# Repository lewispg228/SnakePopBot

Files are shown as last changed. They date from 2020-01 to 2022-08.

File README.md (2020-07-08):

OpenSnake
========================================

<p align="center">
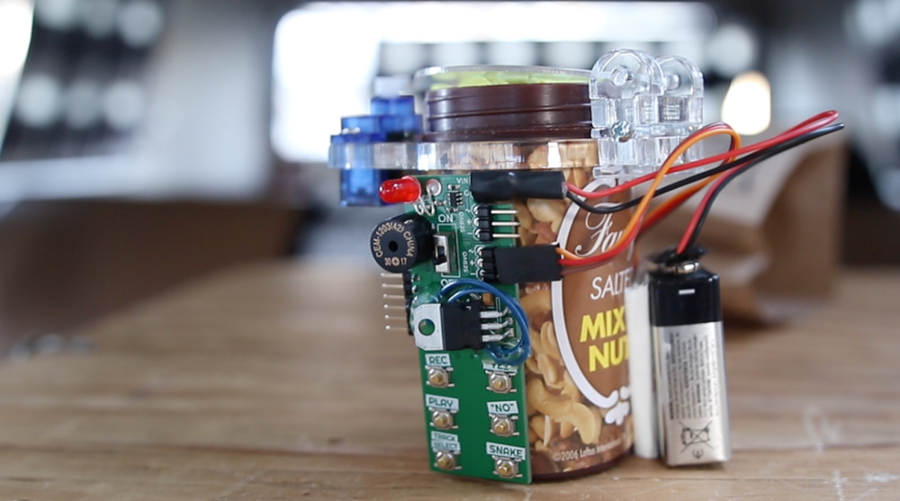
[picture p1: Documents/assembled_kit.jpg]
  
</p>

OpenSnake is the opensource firmware and design files that are used to produce the Electronic Snake In A Can Kit. It is a collaboration between Mario the Maker Magician and Jumping Snakes Engineering.

<p align="center">
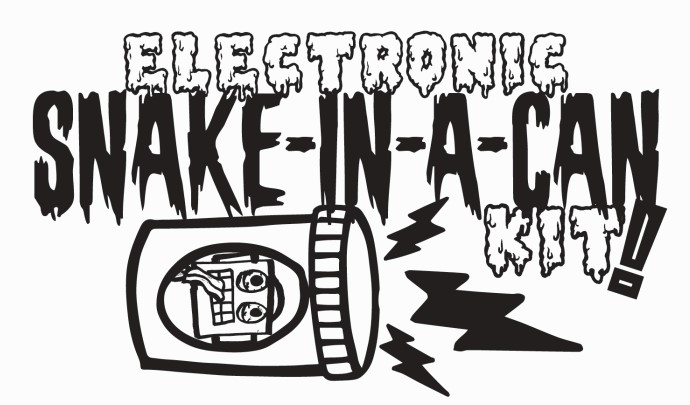
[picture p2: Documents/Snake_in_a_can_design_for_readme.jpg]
  
</p>

The classic snake-in-a-can gag meets DIY MAGIC! With this kit, you'll assemble an Electronic Snake-in-a-Can, introducing you to the world of programming, robotics, and how these tools can be used to create surprise, magic, and comedy.

* includes CONTROLLER for PLAYBACK and RECORDER of robotic magic tricks\
* RE-PROGRAMMABLE with ARDUINO
* learn about SERVOS, BUZZERS, BUTTONS, and LEDs
* pre-programmed with a magic routine written by Mario, PLUS you can make your own
* note: requires 9V battery (not included)

Buy this kit at Mario The Maker Magician's website here:

[BUY KIT HERE](https://www.mariothemagician.com/product-page/electronic-snake-in-a-can-kit)

The magic trick "skit" that is included as track one in the firmware can be watched here on Mario's Instagram post:

[INSTAGRAM VIDEO](https://www.instagram.com/tv/CCRtKZynAKZ/)

Repository Contents
-------------------

* **/Documentation** - assembly instructions, pictures, additional product information
* **/Firmware** - Arduino Code used on the snake-in-a-can controller
* **/Hardware** - Eagle design files (.brd, .sch)
* **/Hardware/Production** - Production panel files (.brd and gerbers)

License Information
-------------------

This product is _**open source**_! 

Please review the LICENSE.md file for license information. 

If you have any questions or concerns on licensing, please [file an issue on this repository](https://github.com/lewispg228/OpenSnake/issues), and we will respond asap.

Distributed as-is; no warranty is given.

- Jumping Snakes Engineering.

_<COLLABORATION CREDIT>_
  
<p align="center">
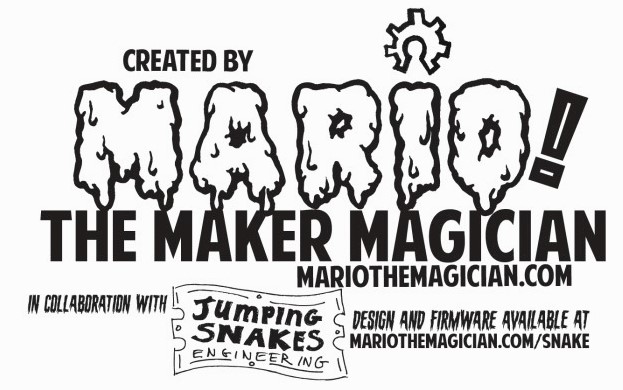
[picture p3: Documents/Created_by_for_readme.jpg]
  
</p>

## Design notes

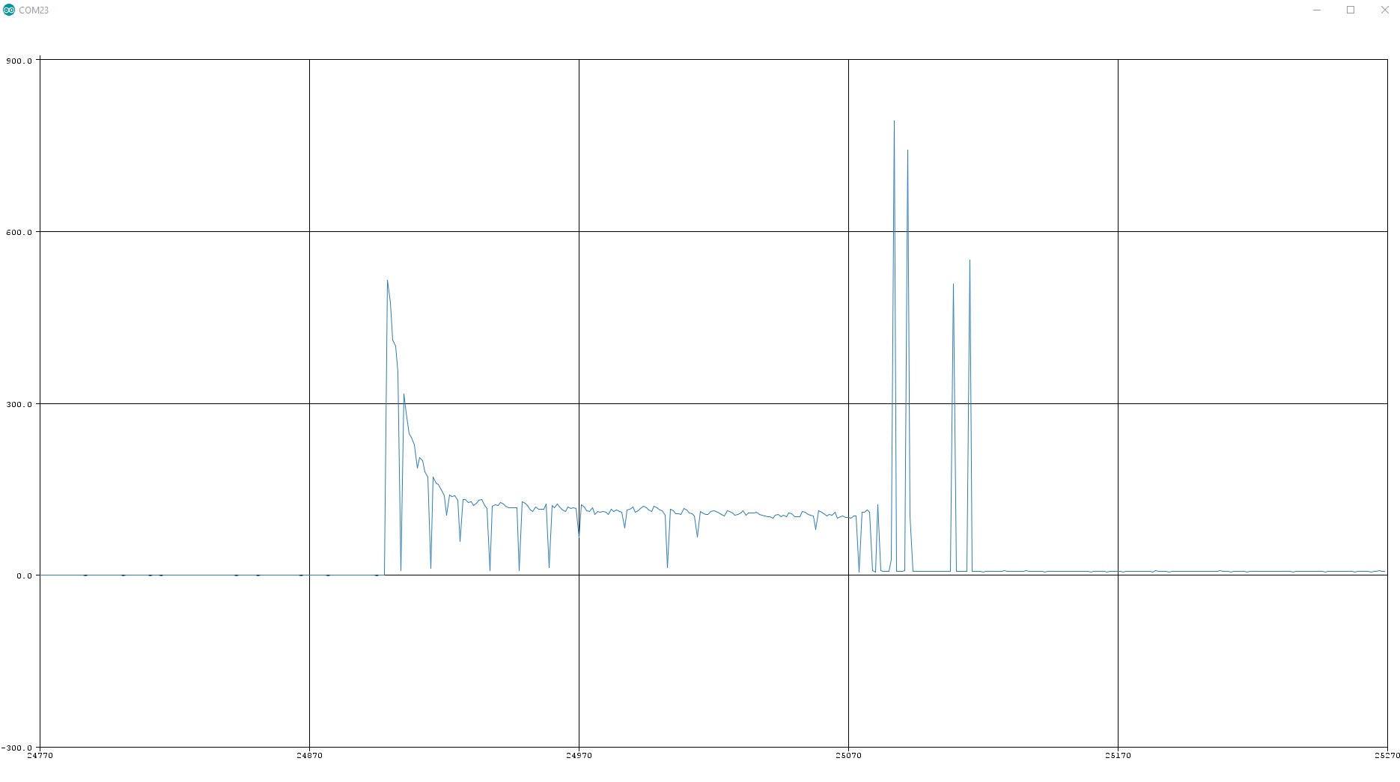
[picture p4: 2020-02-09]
Hardware/Reference/Servo_current spike_standard_size - plug in power and move location.jpg

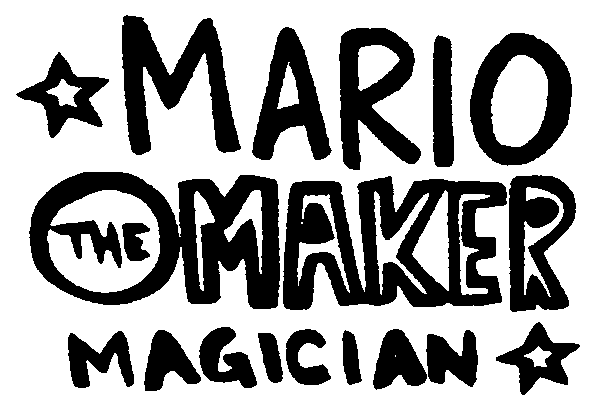
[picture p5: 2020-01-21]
Hardware/Reference/mario2.bmp

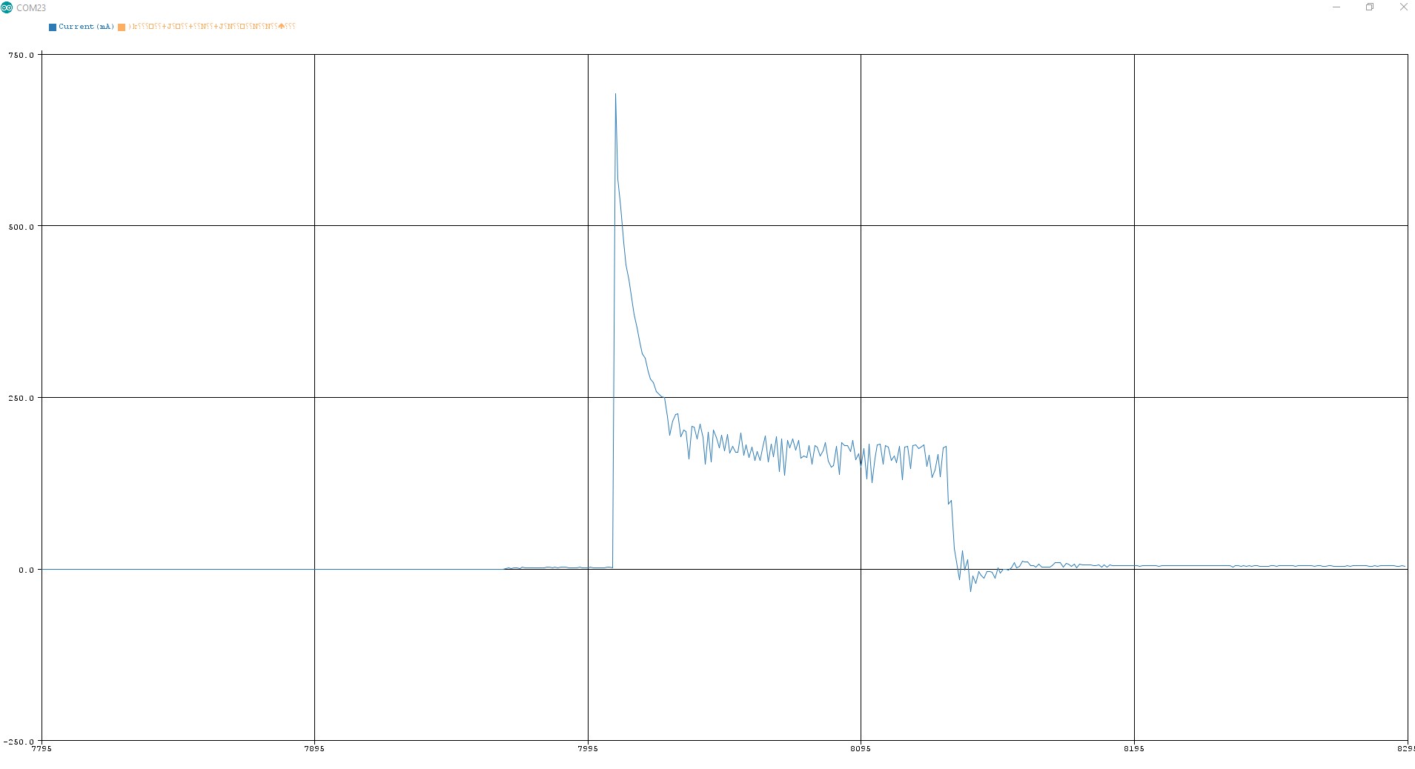
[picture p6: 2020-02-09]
Hardware/Reference/Servo_current spike_MICRO_size - plug in power and move location.jpg

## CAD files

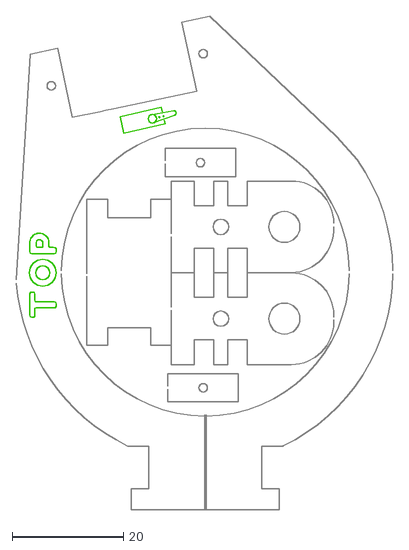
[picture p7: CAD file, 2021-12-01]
Lid/LID.dxf
67.8 x 88.9

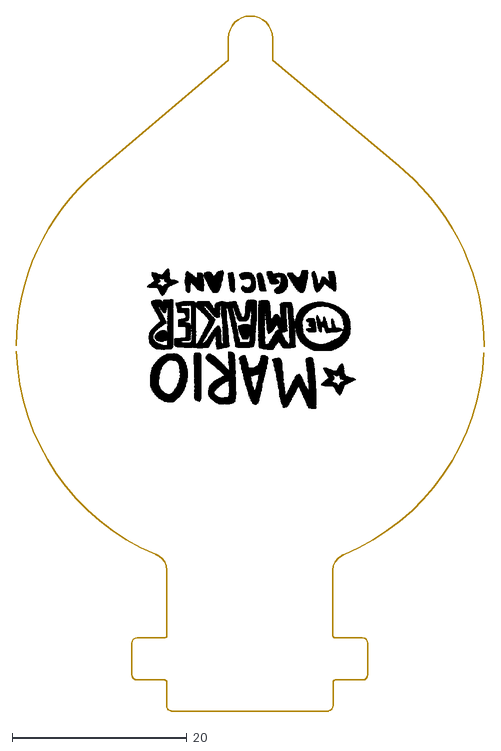
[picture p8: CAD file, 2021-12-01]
Lid/FLAP.dxf
53.7 x 79.6

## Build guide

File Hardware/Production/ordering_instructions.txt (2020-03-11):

panel size, 117x77mm
PCB thickness, 1.6mm
number of layers, 2
soldermask color, Unknown
silkscreen color, White
oz copper, 1oz
finish, HASL lead free
stencils, top+bottom
pcs per panel, 4
min trace width, 0.2540mm / 0.0100in
min drill size, 0.3810mm / 0.0150in

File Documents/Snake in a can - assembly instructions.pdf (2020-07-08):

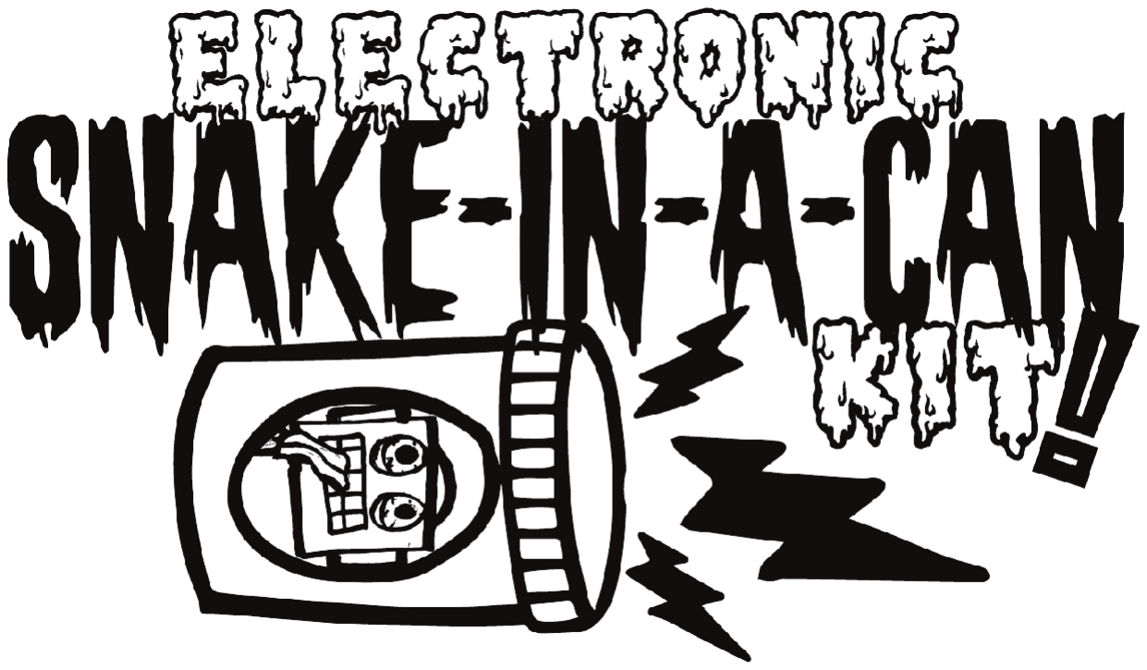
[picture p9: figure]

# Assembly Instructions

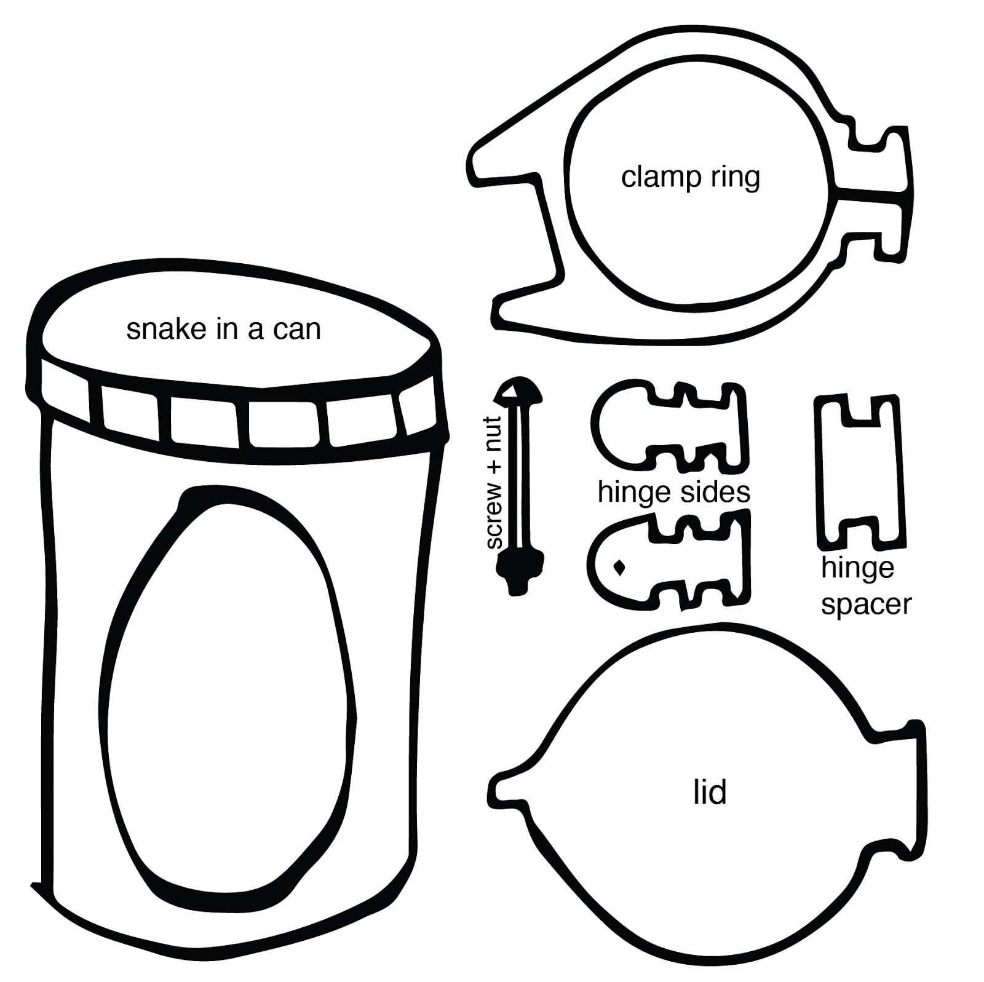
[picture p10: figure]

CAUTION: This kit is designed to be put together with caution and adult supervision.

NEVER POINT THE SNAKE CAN AT ANYONE.

INCLUDES:
1 snake-in-a-can
1 controller (the green thing with buttons and stuff!) 1 can lid assembly
1 servo

REQUIRES:
9V Battery
screw driver
double-sided foam tape or regular duct tape (optional)

ASSEMBLE THE LID

1. Grab these parts:

Snake in a can (1)
Clamp Ring(1)
Hinge sides (2)
Hinge spacer (1)
Lid (1)
Screw (1)
Nut (1)

2. Open the snake can. (Don’t point it at anyone!)
3. Slide the clamp ring all the way up the snake can until it meets the lip of the threads on the can. Make sure it is facing the correct side.
4. Push the hinge sides onto either side of the clamp ring, and position the hinge spacer between the hinge sides.

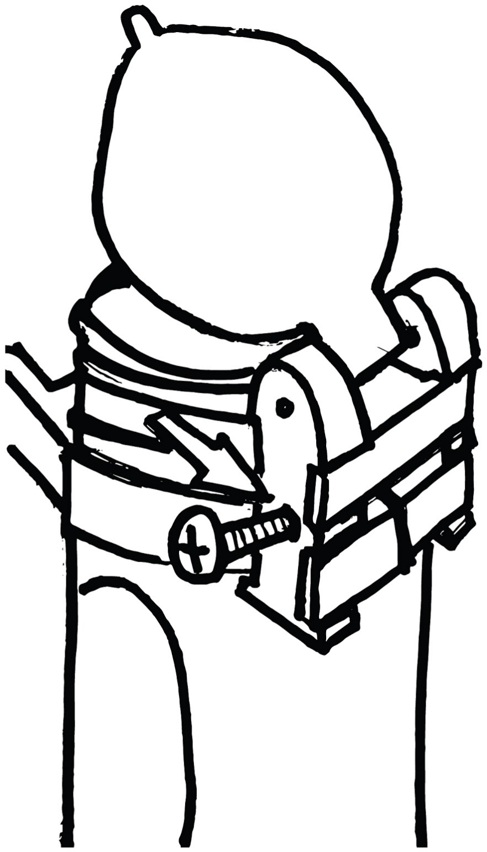
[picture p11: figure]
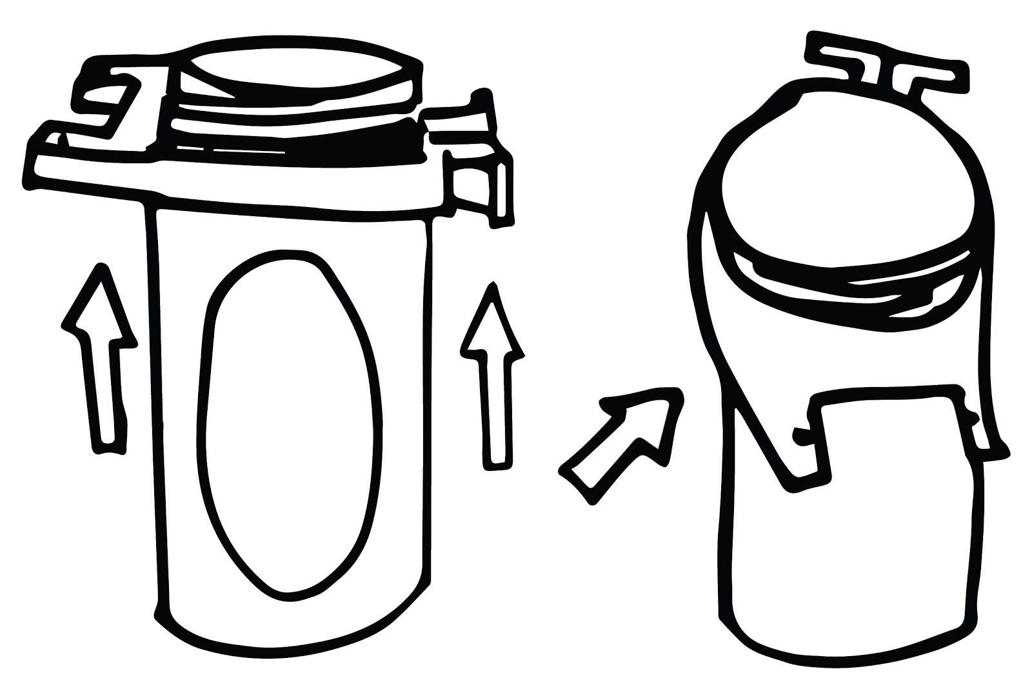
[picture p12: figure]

5. Push the screw through, and loosely tighten the nut on the other end.

Note, the screw and nut are only used to help hold things gently in place right now. No need to tighten it firmly yet.

6. Position the lid between the hinge sides.
7. Tighten the screw and nut to hold the ring in place.

At this point, make the screw and nut really tight. Use a screw driver if necessary.

SERVOS & CABLES

8. Position the servo, and screw it in place. Make sure the white plastic control horn is on the correct side!

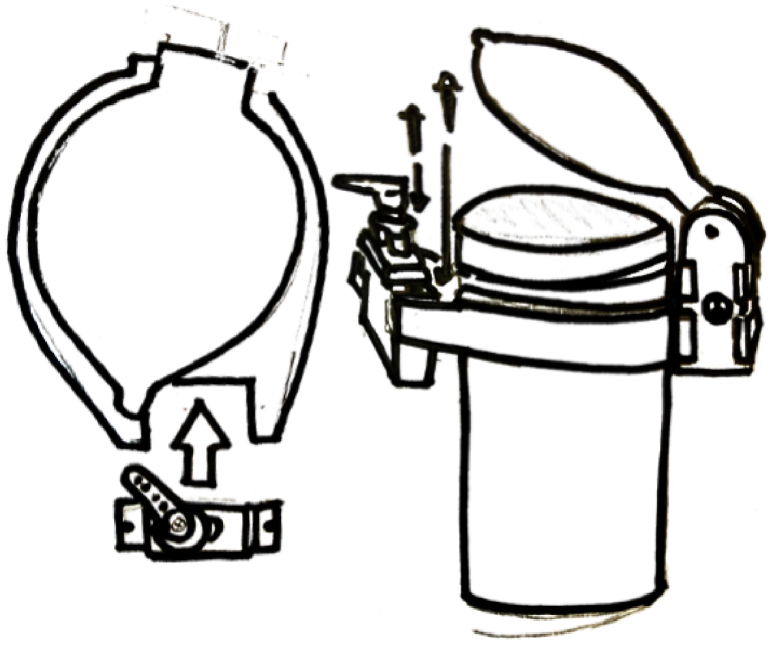
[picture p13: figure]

9. Plug servo cable into controller at “servo 1”. Align the brown wire with the negative sign (“-”).
10. Plug 9V battery into connector.

11. (Optional) Use some double-sided foam tape to attach the controller and battery to the sides of the can.

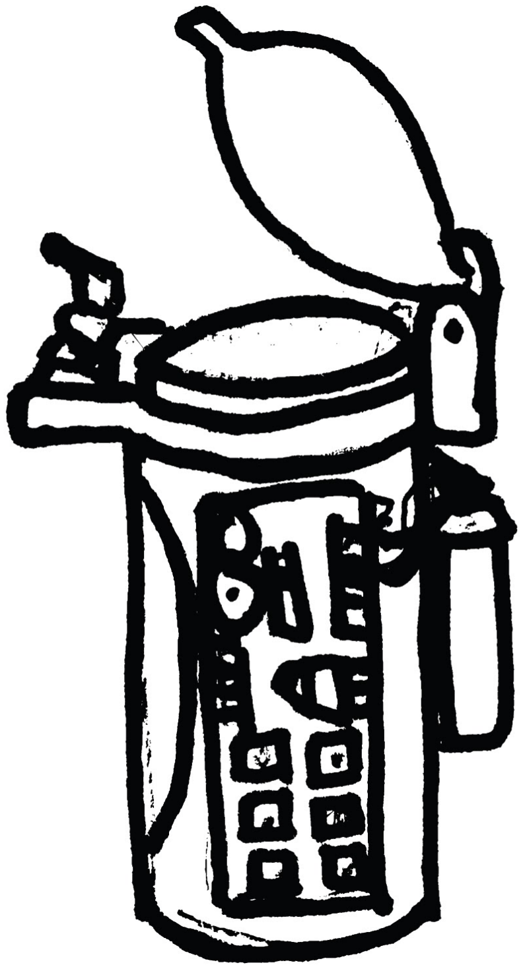
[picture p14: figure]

PREPARE THE SNAKE:

12. Turn the controller OFF.
13. Move servo control horn to the “open” position. (so the horn is over the servo body).
14. Load your spring snake.
15. While holding the lid down, rotate the servo control horn over the lid latch. You want the servo horn to be just over the lid hatch. Just enough for it to hold the lid down
16. Congrats, you have successfully built the kit and are ready to start making magic!

DO MAGIC:

To learn the pre-programmed magic routine and many more advanced features, please visit:

## www.mariothemagician.com/snake

RECORD YOUR OWN:

- Prepare your script… what questions will you ask, and how will the robot answer (YES or NO).
- Turn the controller ON .
- Press TRACK SELECT, and the LED will flash. There are five available tracks. The first track contains the pre-recorded routine above, which can be overwritten. The LED will flash twice for track 2, three times for track 3, etc. Select which track you’d like to record over.
- Press RECORD button once, and the LED will start flashing, indicating record mode.
- Ask your question out loud (to get the timing right) and then press YES or NO or SNAKE.
- When you’re done recording your script, press the
RECORD button again. The LED will stop blinking, indicating that your recording is complete.
- To access your recording, press PLAY.

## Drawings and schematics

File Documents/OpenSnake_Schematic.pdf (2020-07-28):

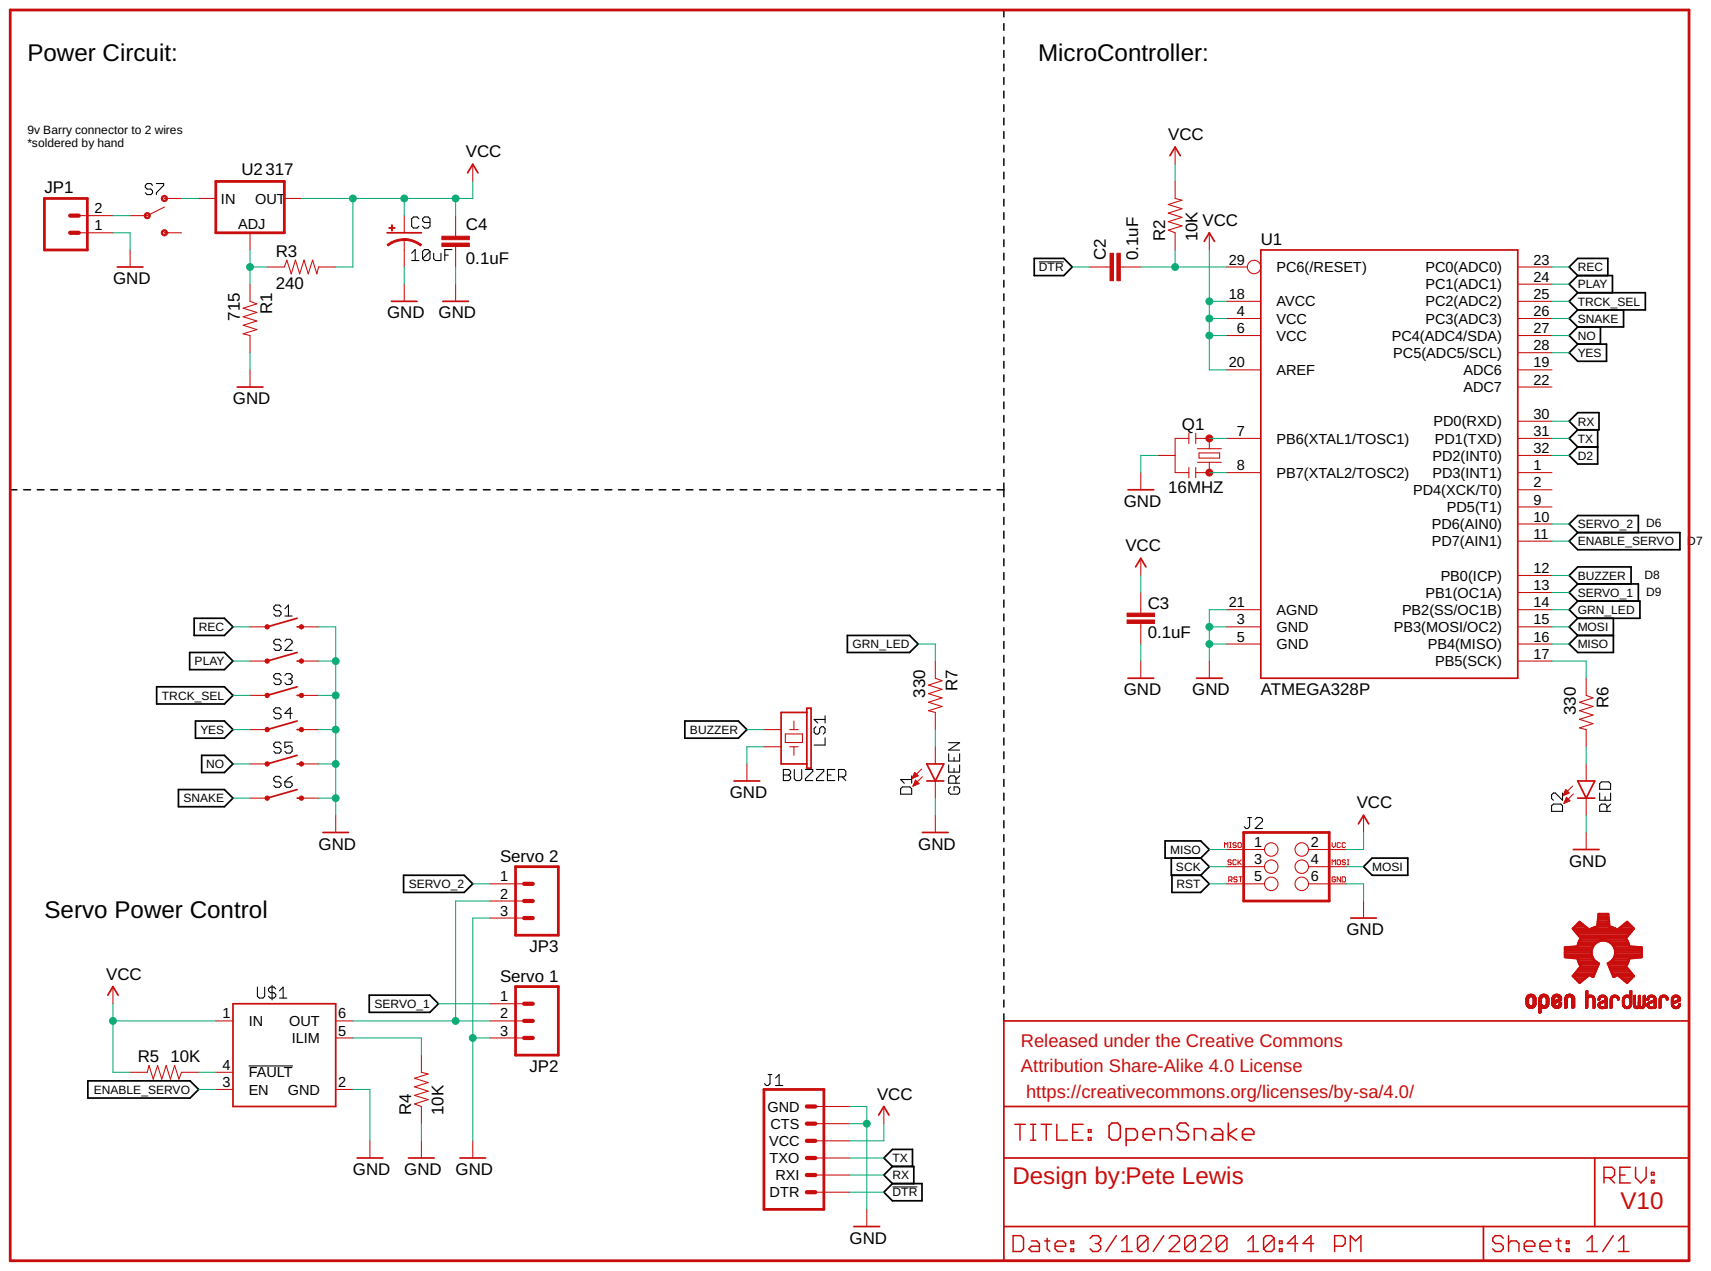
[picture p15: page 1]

9v Barry connector to 2 wires

Released under the Creative Commons
Attribution Share-Alike 4.0 License
https://creativecommons.org/licenses/by-sa/4.0/

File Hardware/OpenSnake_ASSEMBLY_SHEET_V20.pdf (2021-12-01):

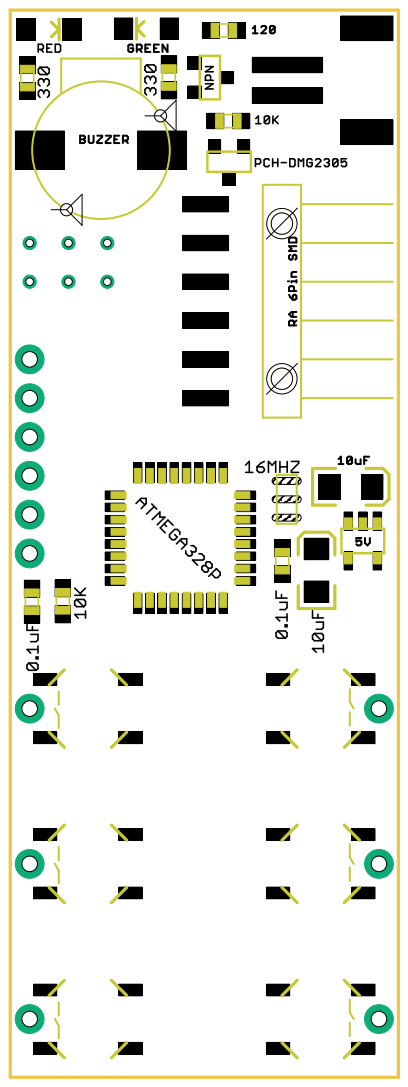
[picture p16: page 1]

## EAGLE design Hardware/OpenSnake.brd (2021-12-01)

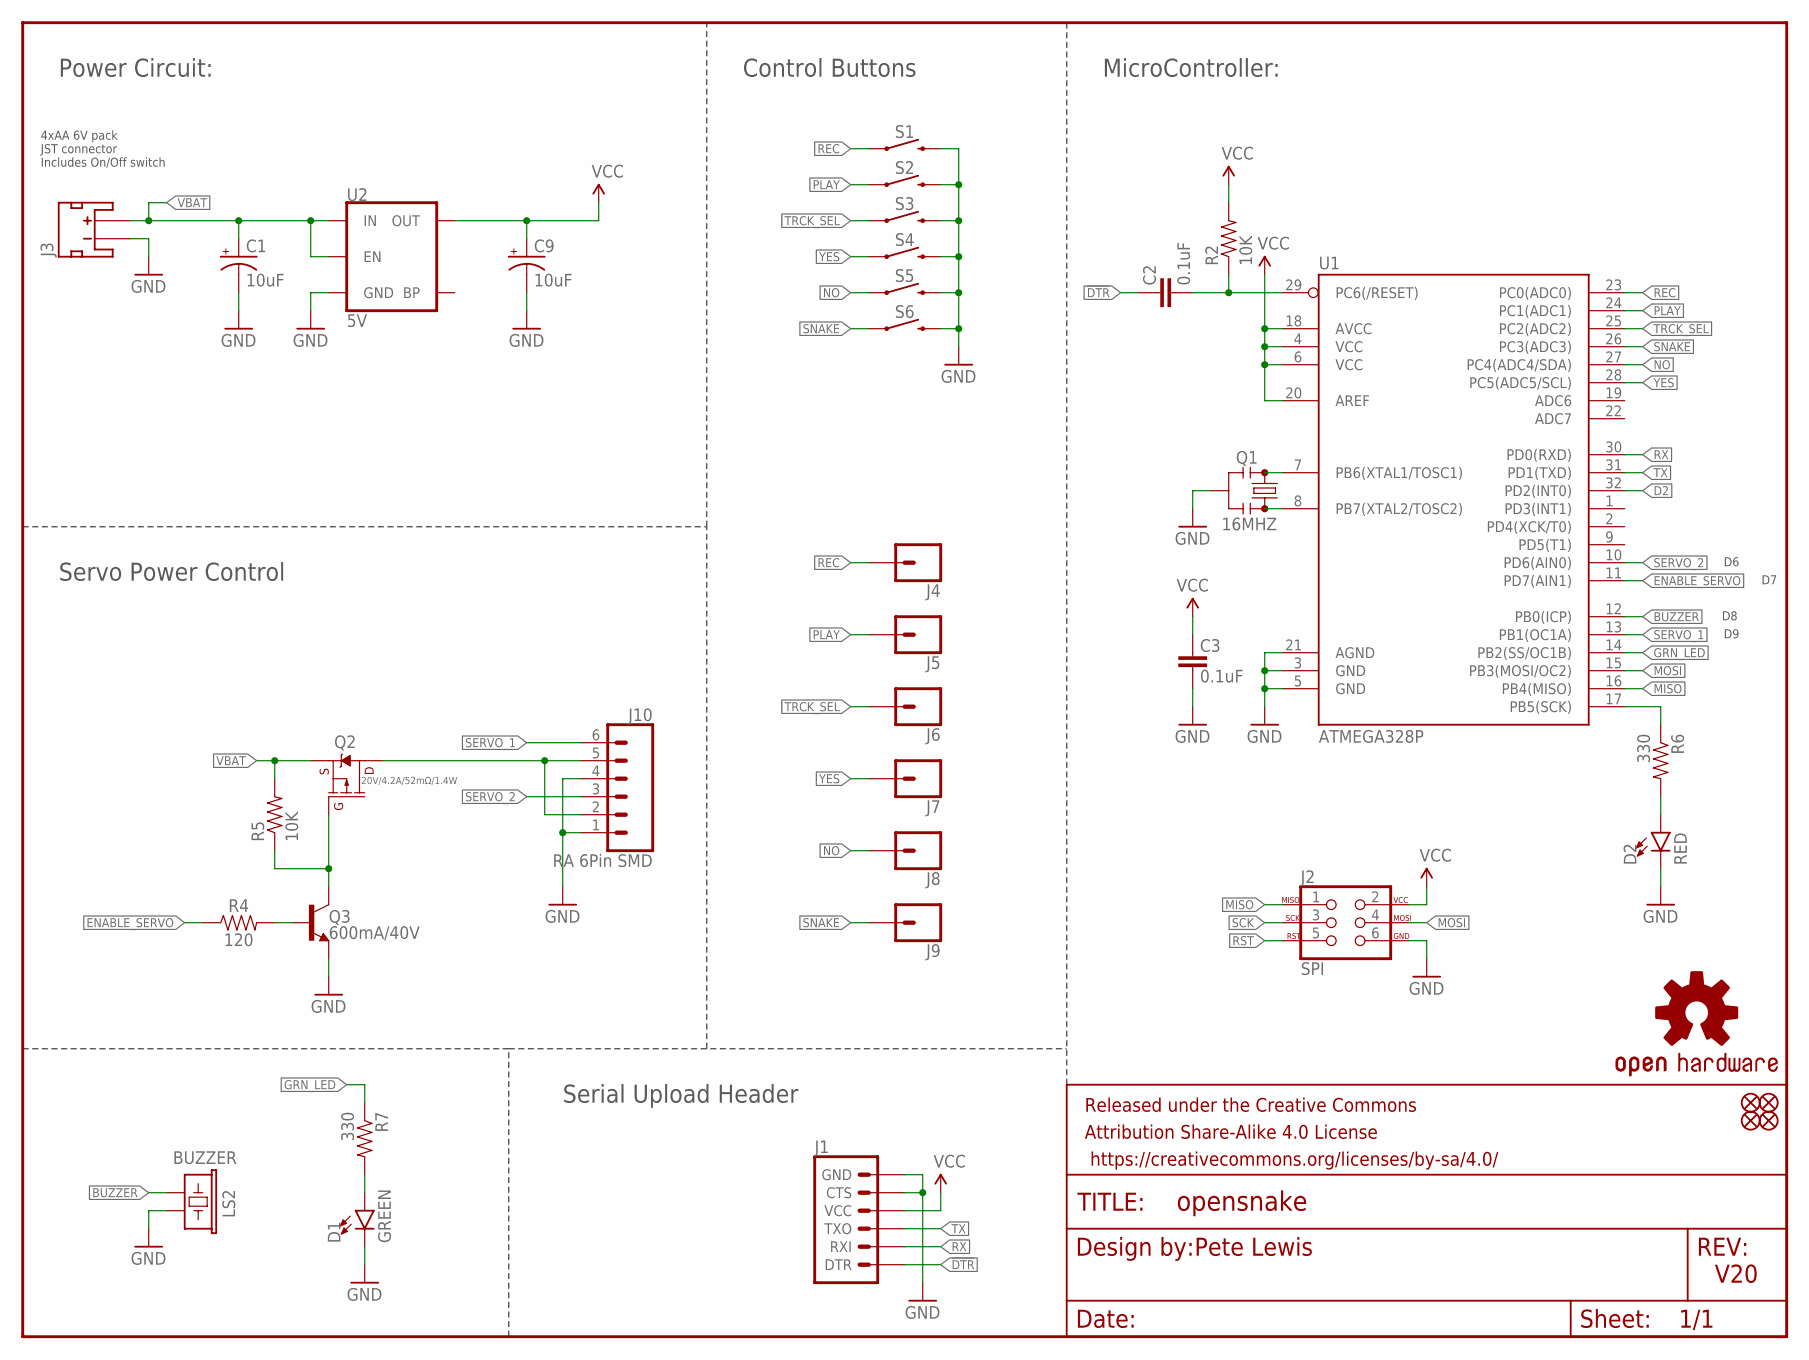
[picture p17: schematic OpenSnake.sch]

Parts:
C1, C9: 10uF; EIA3216
C2, C3: 0.1uF; 0603-CAP
D1: GREEN; LED-1206
D2: RED; LED-1206
FD1, FD2, FD3, FD4: FIDUCIALUFIDUCIAL; FIDUCIAL-MICRO
FRAME1: FRAME-LETTER; CREATIVE_COMMONS
J1: 6_PIN_SERIAL_TARGETSILK; 6_PIN_SERIAL_TARGET_SIDE_W_SILK
J2: SPI; 2X3_TEST_POINTS
J3: JST_2MM_MALE; JST-2-SMD
J4, J5, J6, J7, J8, J9: CONN_01PTH_NO_SILK_YES_STOP; 1X01_NO_SILK
J10: RA 6Pin SMD; 1X06-SMD_RA_MALE
LOGO1: OSHW-LOGOL; OSHW-LOGO-L
LS2: BUZZER; BUZZER-CCV
Q1: 16MHZ; RESONATOR-SMD
Q2: 20V/4.2A/52mΩ/1.4W; SOT23-3
Q3: 600mA/40V; SOT23-3
R2, R5: 10K; 0603-RES
R4: 120; 0603
R6, R7: 330; 0603-RES
S1, S2, S3, S4, S5, S6: MOMENTARY-SWITCH-SPST-SMD-5.2MM-TALL; TACTILE_SWITCH_SMD_5.2MM
U1: ATMEGA328P; TQFP32-08
U2: 5V; SOT23-5

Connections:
!DTR: C2.2, J1.P$1 (DTR)
BUZZER: LS2.- (2), U1.12 (PB0(ICP))
D2: U1.32 (PD2(INT0))
ENABLE_SERVO: R4.1, U1.11 (PD7(AIN1))
GND: C1.-, C3.1, C9.-, D1.C, D2.C, J1.P$5 (CTS), J1.P$6 (GND), J2.6, J3.1 (-), J10.1, J10.4, LS2.+ (1), Q1.2, Q3.2 (E), S1.3 (2), S2.3 (2), S3.3 (2), S4.3 (2), S5.3 (2), S6.3 (2), U1.3 (GND), U1.5 (GND), U1.21 (AGND), U2.2 (GND)
GRN_LED: R7.1, U1.14 (PB2(SS/OC1B))
MISO: J2.1, U1.16 (PB4(MISO))
MOSI: J2.4, U1.15 (PB3(MOSI/OC2))
unnamed: Q1.1, U1.8 (PB7(XTAL2/TOSC2))
unnamed: Q1.3, U1.7 (PB6(XTAL1/TOSC1))
unnamed: Q3.1 (B), R4.2
unnamed: Q2.1 (G), Q3.3 (C), R5.1
unnamed: J10.2, J10.5, Q2.3 (D)
unnamed: D2.A, R6.2
unnamed: D1.A, R7.2
NO: J8.1, S5.1, U1.27 (PC4(ADC4/SDA))
PLAY: J5.1, S2.1, U1.24 (PC1(ADC1))
REC: J4.1, S1.1, U1.23 (PC0(ADC0))
RST: C2.1, J2.5, R2.1, U1.29 (PC6(/RESET))
RX: J1.P$3 (RXI), U1.30 (PD0(RXD))
SCK: J2.3, R6.1, U1.17 (PB5(SCK))
SERVO_1: J10.6, U1.13 (PB1(OC1A))
SERVO_2: J10.3, U1.10 (PD6(AIN0))
SNAKE: J9.1, S6.1, U1.26 (PC3(ADC3))
TRCK_SEL: J6.1, S3.1, U1.25 (PC2(ADC2))
TX: J1.P$2 (TXO), U1.31 (PD1(TXD))
VBAT: C1.+, J3.2 (+), Q2.2 (S), R5.2, U2.1 (IN), U2.3 (EN)
VCC: C3.2, C9.+, J1.P$4 (VCC), J2.2, R2.2, U1.4 (VCC), U1.6 (VCC), U1.18 (AVCC), U1.20 (AREF), U2.5 (OUT)
YES: J7.1, S4.1, U1.28 (PC5(ADC5/SCL))

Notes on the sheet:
V20
Pete Lewis
Power Circuit:
4xAA 6V pack JST connector Includes On/Off switch
MicroController:
Servo Power Control
Control Buttons
Serial Upload Header

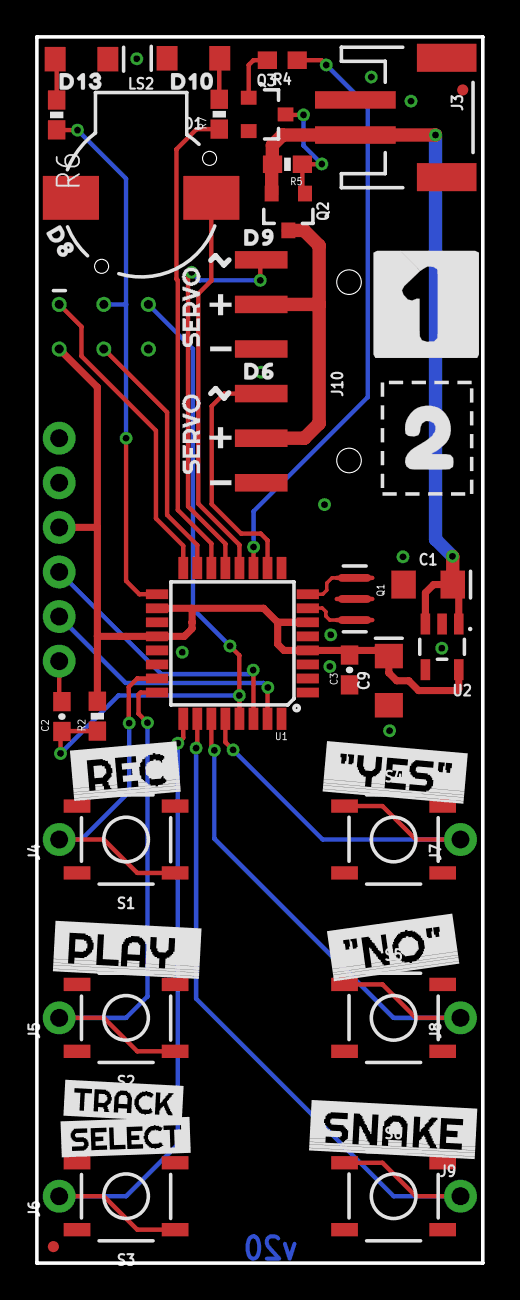
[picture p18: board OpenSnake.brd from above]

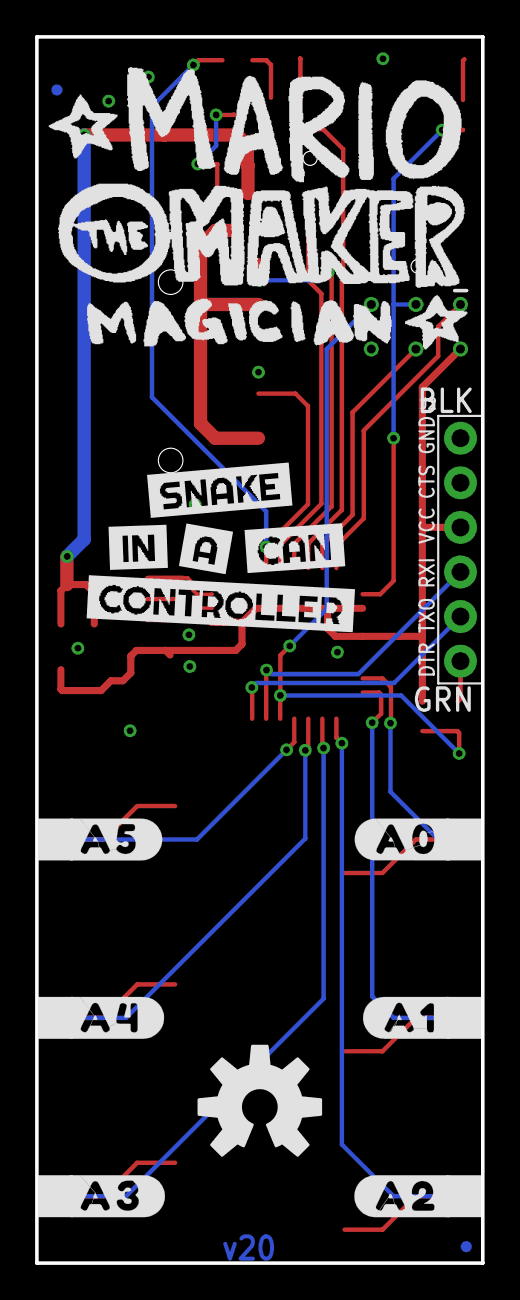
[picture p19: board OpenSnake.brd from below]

Board: 2 copper layers, 25.4 x 69.8 mm, 69 parts (17 on the bottom side), 28 nets.

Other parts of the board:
U$1: #A0#0
U$2: #YES#0
U$3: #NO#1
U$4: SNAKE2
U$5: MARIO_LOGO
U$6: #A1#0
U$7: #A2#0
U$8, U$13: SERVO2
U$9: #A3#0
U$10: #A4#0
U$11, U$12: #1
U$14: SNAKE0
U$15: CONTROLLER4
U$16: IN1
U$17: #A5#0
U$18: D90
U$19: REC0
U$20: PLAY_1
U$21: TRACK2
U$22: SELECT3
U$23: A2
U$24: CAN3
U$25: D60
U$26: D100
U$27: D130
U$28: D80
U$29: #1#0
U$31: 2_0

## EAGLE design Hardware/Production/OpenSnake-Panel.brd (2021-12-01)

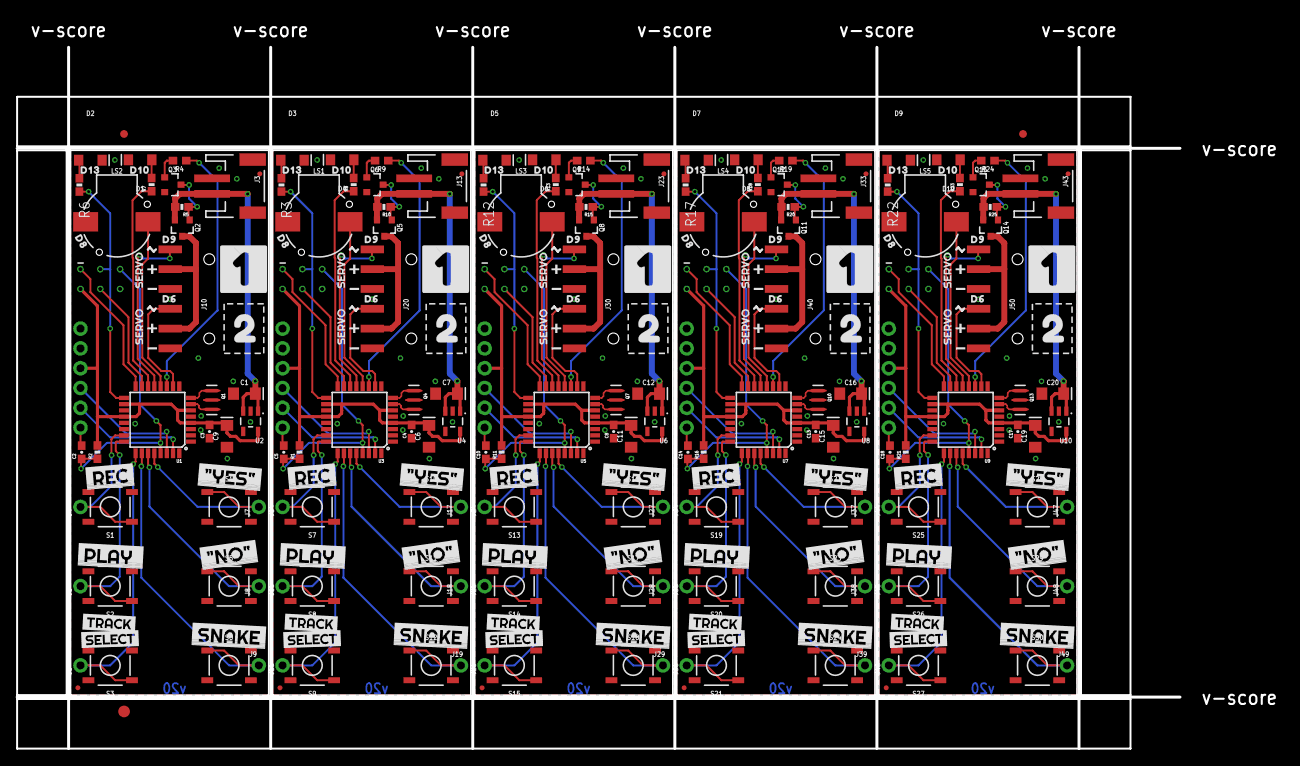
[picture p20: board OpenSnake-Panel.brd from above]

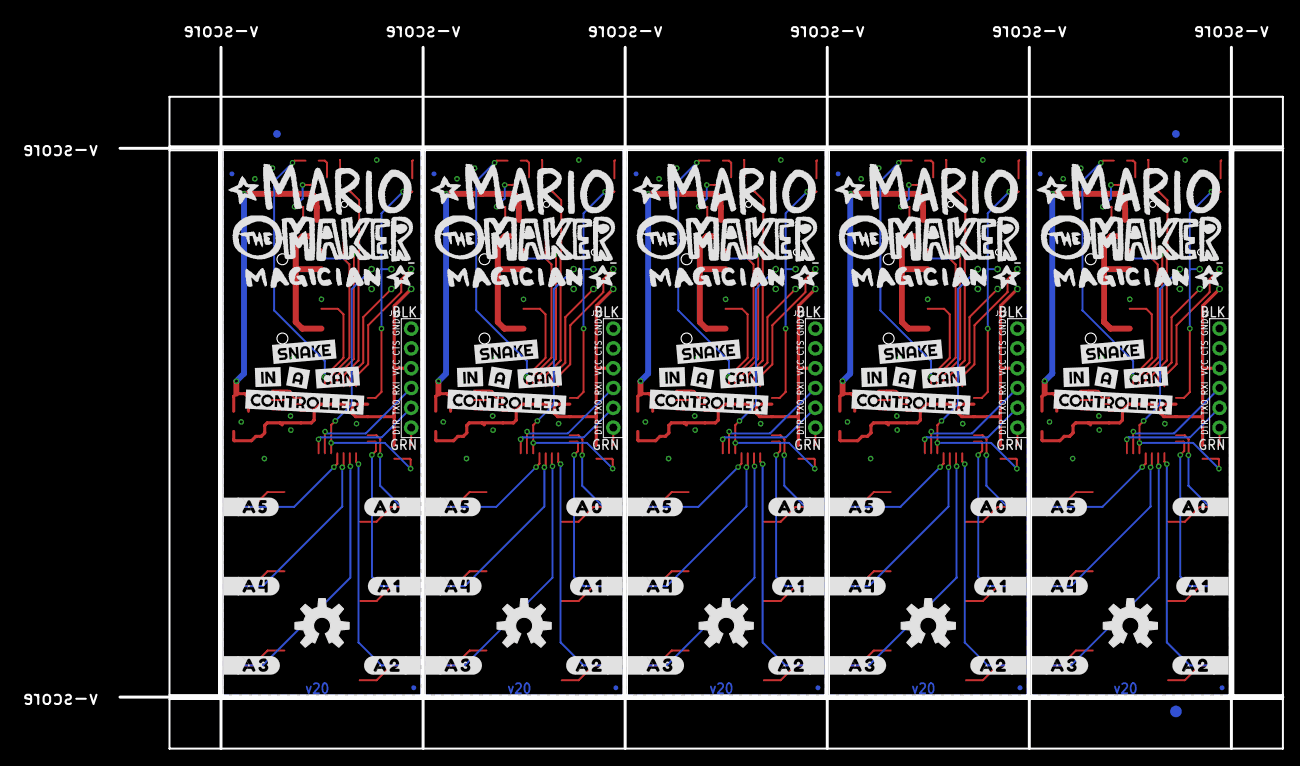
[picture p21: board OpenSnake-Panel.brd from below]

Board: 2 copper layers, 149.1 x 89.9 mm, 346 parts (88 on the bottom side), 140 nets.

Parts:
C1, C6, C7, C9, C11, C12, C15, C16, C19, C20: 10uF; EIA3216
C2, C3, C4, C5, C8, C10, C13, C14, C17, C18: 0.1uF; 0603-CAP
D1, D4, D6, D8, D10: GREEN; LED-1206
D2, D3, D5, D7, D9: RED; LED-1206
E$1, E$2, E$3, E$4: FIDUCIAL-1X2
E$5, E$6: FIDUCIAL-1.5X3
FD1, FD2, FD3, FD4, FD5, FD6, FD7, FD8, FD9, FD10, FD11, FD12, FD13, FD14, FD15, FD16, FD17, FD18, FD19, FD20: FIDUCIALUFIDUCIAL; FIDUCIAL-MICRO
J1, J11, J21, J31, J41: 6_PIN_SERIAL_TARGET_SIDE_W_SILK
J2, J12, J22, J32, J42: SPI; 2X3_TEST_POINTS
J3, J13, J23, J33, J43: JST-2-SMD
J4, J5, J6, J7, J8, J9, J14, J15, J16, J17, J18, J19, J24, J25, J26, J27, J28, J29, J34, J35, J36, J37, J38, J39, J44, J45, J46, J47, J48, J49: 1X01_NO_SILK
J10, J20, J30, J40, J50: RA 6Pin SMD; 1X06-SMD_RA_MALE
LOGO1, LOGO2, LOGO3, LOGO4, LOGO5: OSHW-LOGOL; OSHW-LOGO-L
LS1, LS2, LS3, LS4, LS5: BUZZER; BUZZER-CCV
Q1, Q4, Q7, Q10, Q13: 16MHZ; RESONATOR-SMD
Q2, Q5, Q8, Q11, Q14: 20V/4.2A/52mΩ/1.4W; SOT23-3
Q3, Q6, Q9, Q12, Q15: 600mA/40V; SOT23-3
R1, R2, R5, R10, R11, R15, R16, R20, R21, R25: 10K; 0603-RES
R3, R6, R7, R8, R12, R13, R17, R18, R22, R23: 330; 0603-RES
R4, R9, R14, R19, R24: 100; 0603
S1, S2, S3, S4, S5, S6, S7, S8, S9, S10, S11, S12, S13, S14, S15, S16, S17, S18, S19, S20, S21, S22, S23, S24, S25, S26, S27, S28, S29, S30: TACTILE_SWITCH_SMD_5.2MM
U1, U3, U5, U7, U9: ATMEGA328P; TQFP32-08
U2, U4, U6, U8, U10: 5V; SOT23-5
U$1, U$48, U$78, U$108, U$138: #A0#0
U$2, U$30, U$61, U$91, U$121: #YES#0
U$3, U$32, U$62, U$92, U$122: #NO#1
U$4, U$33, U$63, U$93, U$123: SNAKE2
U$5, U$38, U$68, U$98, U$128: MARIO_LOGO
U$6, U$49, U$79, U$109, U$139: #A1#0
U$7, U$50, U$80, U$110, U$140: #A2#0
U$8, U$13, U$41, U$42, U$71, U$72, U$101, U$102, U$131, U$132: SERVO2
U$9, U$51, U$81, U$111, U$141: #A3#0
U$10, U$52, U$82, U$112, U$142: #A4#0
U$11, U$12, U$39, U$40, U$69, U$70, U$99, U$100, U$129, U$130: #1
U$14, U$43, U$73, U$103, U$133: SNAKE0
U$15, U$47, U$77, U$107, U$137: CONTROLLER4
U$16, U$44, U$74, U$104, U$134: IN1
U$17, U$53, U$83, U$113, U$143: #A5#0
U$18, U$54, U$84, U$114, U$144: D90
U$19, U$34, U$64, U$94, U$124: REC0
U$20, U$35, U$65, U$95, U$125: PLAY_1
U$21, U$36, U$66, U$96, U$126: TRACK2
U$22, U$37, U$67, U$97, U$127: SELECT3
U$23, U$45, U$75, U$105, U$135: A2
U$24, U$46, U$76, U$106, U$136: CAN3
U$25, U$55, U$85, U$115, U$145: D60
U$26, U$56, U$86, U$116, U$146: D100
U$27, U$57, U$87, U$117, U$147: D130
U$28, U$58, U$88, U$118, U$148: D80
U$29, U$59, U$89, U$119, U$149: #1#0
U$31, U$60, U$90, U$120, U$150: 2_0

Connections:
!DTR: C2.2, J1.P$1
!DTR1: C5.2, J11.P$1
!DTR2: C10.2, J21.P$1
!DTR3: C14.2, J31.P$1
!DTR4: C18.2, J41.P$1
BUZZER: LS2.-, U1.12
BUZZER1: LS1.-, U3.12
BUZZER2: LS3.-, U5.12
BUZZER3: LS4.-, U7.12
BUZZER4: LS5.-, U9.12
ENABLE_SERVO: R4.1, U1.11
ENABLE_SERVO1: R9.1, U3.11
ENABLE_SERVO2: R14.1, U5.11
ENABLE_SERVO3: R19.1, U7.11
ENABLE_SERVO4: R24.1, U9.11
GND: C1.-, C3.1, C9.-, D1.C, D2.C, J1.P$5, J1.P$6, J2.6, J3.1, J10.1, J10.4, LS2.+, Q1.2, Q3.2, S1.3, S2.3, S3.3, S4.3, S5.3, S6.3, U1.3, U1.5, U1.21, U2.2
GND1: C4.1, C6.-, C7.-, D3.C, D4.C, J11.P$5, J11.P$6, J12.6, J13.1, J20.1, J20.4, LS1.+, Q4.2, Q6.2, S7.3, S8.3, S9.3, S10.3, S11.3, S12.3, U3.3, U3.5, U3.21, U4.2
GND2: C8.1, C11.-, C12.-, D5.C, D6.C, J21.P$5, J21.P$6, J22.6, J23.1, J30.1, J30.4, LS3.+, Q7.2, Q9.2, S13.3, S14.3, S15.3, S16.3, S17.3, S18.3, U5.3, U5.5, U5.21, U6.2
GND3: C13.1, C15.-, C16.-, D7.C, D8.C, J31.P$5, J31.P$6, J32.6, J33.1, J40.1, J40.4, LS4.+, Q10.2, Q12.2, S19.3, S20.3, S21.3, S22.3, S23.3, S24.3, U7.3, U7.5, U7.21, U8.2
GND4: C17.1, C19.-, C20.-, D9.C, D10.C, J41.P$5, J41.P$6, J42.6, J43.1, J50.1, J50.4, LS5.+, Q13.2, Q15.2, S25.3, S26.3, S27.3, S28.3, S29.3, S30.3, U9.3, U9.5, U9.21, U10.2
GRN_LED: R7.1, U1.14
GRN_LED1: R8.1, U3.14
GRN_LED2: R13.1, U5.14
GRN_LED3: R18.1, U7.14
GRN_LED4: R23.1, U9.14
MISO: J2.1, U1.16
MISO1: J12.1, U3.16
MISO2: J22.1, U5.16
MISO3: J32.1, U7.16
MISO4: J42.1, U9.16
MOSI: J2.4, U1.15
MOSI1: J12.4, U3.15
MOSI2: J22.4, U5.15
MOSI3: J32.4, U7.15
MOSI4: J42.4, U9.15
unnamed: Q1.1, U1.8
unnamed: Q1.3, U1.7
unnamed: D3.A, R3.2
unnamed: Q3.1, R4.2
unnamed: Q2.1, Q3.3, R5.1
unnamed: J10.2, J10.5, Q2.3
unnamed: D2.A, R6.2
unnamed: Q4.1, U3.8
unnamed: Q4.3, U3.7
unnamed: D1.A, R7.2
unnamed: J20.2, J20.5, Q5.3
unnamed: D4.A, R8.2
unnamed: Q6.1, R9.2
unnamed: Q5.1, Q6.3, R10.1
unnamed: D5.A, R12.2
unnamed: Q7.1, U5.8
unnamed: Q7.3, U5.7
unnamed: J30.2, J30.5, Q8.3
unnamed: D6.A, R13.2
unnamed: Q9.1, R14.2
unnamed: Q8.1, Q9.3, R15.1
unnamed: D7.A, R17.2
unnamed: Q10.1, U7.8
unnamed: Q10.3, U7.7
unnamed: J40.2, J40.5, Q11.3
unnamed: D8.A, R18.2
unnamed: Q12.1, R19.2
unnamed: Q11.1, Q12.3, R20.1
unnamed: D9.A, R22.2
unnamed: Q13.1, U9.8
unnamed: Q13.3, U9.7
unnamed: J50.2, J50.5, Q14.3
unnamed: D10.A, R23.2
unnamed: Q15.1, R24.2
unnamed: Q14.1, Q15.3, R25.1
NO: J8.1, S5.1, U1.27
NO1: J18.1, S11.1, U3.27
NO2: J28.1, S17.1, U5.27
NO3: J38.1, S23.1, U7.27
NO4: J48.1, S29.1, U9.27
PLAY: J5.1, S2.1, U1.24
PLAY1: J15.1, S8.1, U3.24
PLAY2: J25.1, S14.1, U5.24
PLAY3: J35.1, S20.1, U7.24
PLAY4: J45.1, S26.1, U9.24
REC: J4.1, S1.1, U1.23
REC1: J14.1, S7.1, U3.23
REC2: J24.1, S13.1, U5.23
REC3: J34.1, S19.1, U7.23
REC4: J44.1, S25.1, U9.23
RST: C2.1, J2.5, R2.1, U1.29
RST1: C5.1, J12.5, R1.1, U3.29
RST2: C10.1, J22.5, R11.1, U5.29
RST3: C14.1, J32.5, R16.1, U7.29
RST4: C18.1, J42.5, R21.1, U9.29
RX: J1.P$3, U1.30
RX1: J11.P$3, U3.30
RX2: J21.P$3, U5.30
RX3: J31.P$3, U7.30
RX4: J41.P$3, U9.30
SCK: J2.3, R6.1, U1.17
SCK1: J12.3, R3.1, U3.17
SCK2: J22.3, R12.1, U5.17
SCK3: J32.3, R17.1, U7.17
SCK4: J42.3, R22.1, U9.17
SERVO_1: J10.6, U1.13
SERVO_2: J10.3, U1.10
SERVO_3: J20.6, U3.13
SERVO_4: J20.3, U3.10
SERVO_5: J30.6, U5.13
SERVO_6: J30.3, U5.10
SERVO_7: J40.6, U7.13
SERVO_8: J40.3, U7.10
SERVO_9: J50.6, U9.13
SERVO_10: J50.3, U9.10
SNAKE: J9.1, S6.1, U1.26
SNAKE1: J19.1, S12.1, U3.26
SNAKE2: J29.1, S18.1, U5.26
SNAKE3: J39.1, S24.1, U7.26
SNAKE4: J49.1, S30.1, U9.26
TRCK_SEL: J6.1, S3.1, U1.25
TRCK_SEL1: J16.1, S9.1, U3.25
TRCK_SEL2: J26.1, S15.1, U5.25
TRCK_SEL3: J36.1, S21.1, U7.25
TRCK_SEL4: J46.1, S27.1, U9.25
TX: J1.P$2, U1.31
TX1: J11.P$2, U3.31
TX2: J21.P$2, U5.31
TX3: J31.P$2, U7.31
TX4: J41.P$2, U9.31
VBAT: C1.+, J3.2, Q2.2, R5.2, U2.1, U2.3
VBAT1: C7.+, J13.2, Q5.2, R10.2, U4.1, U4.3
VBAT2: C12.+, J23.2, Q8.2, R15.2, U6.1, U6.3
VBAT3: C16.+, J33.2, Q11.2, R20.2, U8.1, U8.3
VBAT4: C20.+, J43.2, Q14.2, R25.2, U10.1, U10.3
VCC: C3.2, C9.+, J1.P$4, J2.2, R2.2, U1.4, U1.6, U1.18, U1.20, U2.5
VCC1: C4.2, C6.+, J11.P$4, J12.2, R1.2, U3.4, U3.6, U3.18, U3.20, U4.5
VCC2: C8.2, C11.+, J21.P$4, J22.2, R11.2, U5.4, U5.6, U5.18, U5.20, U6.5
VCC3: C13.2, C15.+, J31.P$4, J32.2, R16.2, U7.4, U7.6, U7.18, U7.20, U8.5
VCC4: C17.2, C19.+, J41.P$4, J42.2, R21.2, U9.4, U9.6, U9.18, U9.20, U10.5
YES: J7.1, S4.1, U1.28
YES1: J17.1, S10.1, U3.28
YES2: J27.1, S16.1, U5.28
YES3: J37.1, S22.1, U7.28
YES4: J47.1, S28.1, U9.28

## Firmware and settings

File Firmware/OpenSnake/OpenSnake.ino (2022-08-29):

/*
  Snake In A Can Controller
  Written by: Pete Lewis, with contributions from Jeff Haas
  Jumping Snakes Engineering LLC
  A collaboration with Mario the Maker Magician
  https://www.mariothemagician.com/

  Original start date Jan 21st, 2020

  License: MIT. See license file for more information but you can
  basically do whatever you want with this code.

  Jan 12th, 2021
  This firmware also has contributions from Jeff Haas.
  Big thanks for the laughing, crying and happy birthday song code!

  Aug 26th, 2022
  Adding in production testing method.
  To engage, hold down YES through a power cycle.

  Also thanks to the Adafruit animal sounds example code found here:
  https://learn.adafruit.com/adafruit-trinket-modded-stuffed-animal/animal-sounds

  And JSHENGs happy birthday example code found here:
  https://create.arduino.cc/projecthub/jsheng/happy-birthday-lights-and-sounds-1745cd

  This firmware is intended to be used with the Snake in a Can Controller.
  That product, videos and more info can be found here:
  https://www.mariothemagician.com/snake
  Note, it could also be wired up with any Arduino board.
  It allows the user to blink LEDs, buzz sounds, and turn a servo.
  The servo holds the latch on a lid, that can let a spring snake jump out.

  The controller is often placed inside a brown paper lunch bag, and a robot
  face is drawn on the front of the bag. Now you've got a robot that can blink,
  talk (buzz) and pop a snake!

  With these elements in the design, a performer (most likely a magician)
  can perform a skit using this controller as a robot to interact with.
  By timing the events of various buzz sounds, LED blinks, and snake pops,
  the robot can now be part of the show.

  The controller comes pre-programmed with one skit that Mario the Maker has
  written. Visit https://mariothemagician.com/snake to watch a video, learn the
  magic show and perform it yourself!

  You can also write your own magic shows using the on-board recording buttons.
  See the USER INTERFACE comments below.

  /////////////// USER INTERFACE //////////////////////////////////////////////////////////

  To play a track:
  Turn on power.
  User sees current track number blink on LED.
  Press PLAY to play track.

  To select a different track:
  Turn on power.
  User sees current track number blink on LED.
  Prest TRACK SELECT (hold down for 3 seconds) to change tracks.
    -When you press this button, it will increment the current track
    -It will also "loop back around" to track 1, when you reach the end and press it again.
    -Each time you press it, you will see the current track number blink on the LED

  To Record a new track:
  Note, you can record over the current track, or you can increment to an empty track.
  Select desired track you wish to record on (or over).
  Press REC (hold for 3 seconds) to begin recording.
  Press "YES", "NO", and "SNAKE" as desired.
    -It is recommended that you write out your skit, and then just read the lines as you record
  Press REC again to stop recording.
  Now your new track is avaialable for playback.

     Note, new sounds have been added into firmware version 1.1
     Crying, laughing and happy birthday.
     To access these additional sounds, you must hold down the "TRACK SELECT" button before
     pressing the other buttons. The "TRACK SELECT" button acts like a "shift" key.
     TRACK SELECT + YES = LAUGH
     TRACK SELECT + NO = CRY
     TRACK SELECT + SNAKE = HAPPY BIRTHDAY

  FACTORY RESET
  If you do not want to keep your current tracks,
  and would like to restore the original Mario example track,
  (1) Turn unit OFF
  (2) Press and Hold REC button
  (3) Turn the unit ON (while continuing to hold down REC)
  (4) Watch for 3 red blinks
  (5) Release button
  Now your controller has been set back to it's orginal track and your other tracks have been cleared.

  AUTOPLAY
  When autoplay is engaged, your controller will begin the selected track on power up (without requiring you to press the PLAY button).
  This is useful for performances, because you can more easily access the power slide switch (on the battery pack).
  To turn on autoplay:
  (1) Turn unit OFF
  (2) Press and Hold PLAY button
  (3) Turn the unit ON (while continuing to hold down PLAY)
  (4) Watch for 3 green blinks
  (5) Release button
  Now autoplay has been engaged. Each time you power on your controller, it will begin the selected track.
  To turn off autoplay (aka go back into "normal mode"):
  Repeat the process above.
  Note, each time you do the process above it will effectivly "toggle" autoplay on or off.
  Also, a factory_reset() will also set autoplay to OFF.

  ///////////////  EEPROM NOTES //////////////////////////////////////////////////////////

  We will use EEPROM to store "tracks"
  A track is a recorded sequence of events.
  Each event is a button press, which will have a timestamp and a type
  timestamps will be a value from 0-255
  a timestamp will represent seconds in 2.1 format
  for example 010 is 1.0 seconds, 215 is 21.5 seconds
  This means that the longest timestamp possible is 25.5 seconds

  Events will be either "yes", "no", "snake", or "end"
  These will be represented by the values 1,2, or 3.
  More event types might come later.

  A track consists of a sequence of timestamps and event types.

  NOTE!! EEPROM location 0 is special and will contain the selected track.

  EEPROM location 1023 is special and will tell us if this is a fresh IC.
  Fresh ICs come with all EEPROM set to 255, so that means we need to do a factory reset.
  After we do a factory reset, then we will set location 1023 to a 1, indicating that this is no longer
  a fresh chip.
  To cause a factory reset, we will simply write location 1023 to 255, and require a power cycle reset.

  EEPROM locations 1-101 will be track 1.
  For example a track might look like this:
  010, 001, 010, 002, 025, 003
  This track would pause 1.0 seconds,
  Then play a "yes"
  Pause for 1.0 seconds,
  Them play a "no"
  Pause for 2.5 seconds
  Then pop open the snake.

  NOTE, each track can have 50 events.
  NOTE, we will allow for 5 tracks, so that will requres 500 memory locations.
  The ATMEGA328 has 1000 EEPROM locations, so we should be fine.

  Mario's original example track will be stored in track 1.
  It is also "backed up" as a variable array in this sketch, and can be restored via factory_reset().


  /////////////// HARDWARE SETUP //////////////////////////////////////////////////////////

  Micro:      ATEMGA328
  Ext osc:    16 MHz
  Brownout:   2.7V
  HIGH FUSE:  0xDE
  LOW FUSE:   0xFF
  EXT FUSE:   0xFD
  LOCK:       0xCF
  Bootloader: Optiboot
  Board select: Arduino/Genuino Uno

*/

#include <Servo.h>

Servo myservo;  // create servo object to control a servo

#include <EEPROM.h>

#define EEPROM_LOCATION_TRACK 0 // to store which track we have selected, 0-5
#define EEPROM_LOCATION_AUTOPLAY 1023 // to store if we're in Autoplay (1) or not (0)
#define AUTOPLAY_ON 1
#define AUTOPLAY_OFF 0

#include "pitches.h" // used for the happy birthday function

// Event types
#define YES 1
#define NO 2
#define SNAKE 3
#define LAUGH 4
#define CRY 5
#define HAPPY 6
#define END 99 // had to choose something, so went with this, wanted to leave room for other future event types

// Control Buttons
#define RECORD_BUTTON A0
#define PLAY_BUTTON A1
#define TRACK_SELECT_BUTTON A2
#define YES_BUTTON A5
#define NO_BUTTON A4
#define SNAKE_BUTTON A3

// User input commands
#define RECORD_CMD 1
#define PLAY_CMD 2
#define TRACK_CMD 3
#define YES_CMD 4
#define NO_CMD 5
#define SNAKE_CMD 6
#define LAUGH_CMD 7
#define CRY_CMD 8
#define HAPPY_CMD 9

byte userInput = 0; // global variable to store current user input command

// button counters, used to accept "long presses" on a button.
// Record and track select are special, they require the user to
// press the button longer (2 seconds?) for it to cause a valid press.
// play is instant effective and will begin the current track instantly,
// because users often want a skit to start playing instantly.
// This is most important to avoid accidental record or track select presses.
//
// Note, snake button was also added in FW ver 1.1 to allow the user to
// cause a snake pop to set the servo horn. If you hold down servo for a
// long press, then it calls the snake function moving the servo to the
// open position.
int recordButtonCounter = 0;
int incrementTrackButtonCounter = 0;
int snakeButtonCounter = 0;


#define SERVO_PWM_PIN 9
#define SERVO_PWR_CONTROL_PIN 7
#define BUZZER_PIN 8

#define RED_LED_pin 13
#define GREEN_LED_pin 10

// example tracks
// they are a sequence of events
// they are formatted like so:
// delay, type, delay, type, and so on... (max 50 events)
// delay values are in 2.1 format, (so 10 = 1.0 second, and 105 = 10.5 seconds)
// this gives you 1/10th of a second precision
// and the max delay is 25.5 seconds (EEPROM stores byte, so values of 0-255).
// all tracks must have a last event delay of 0, followed by an event type END

byte example_track_1[] = {
  56, YES, // first event, delay 5.3 seconds, sound "yes"
  51, YES, // second event, delay 5.1 seconds, sound "yes"
  2, YES,
  72, NO,
  67, NO,
  43, NO,
  55, YES,
  1, YES,
  15, SNAKE, // delay 1.5 seconds, pop the snake
  0, END
};

/* The following example tracks are only here to show how to write
  byte example_track_2[] = {
  20, YES,
  20, NO,
  20, YES,
  20, NO,
  30, SNAKE,
  0, END
  };

  byte example_track_3[] = {
  30, YES,
  30, YES,
  30, YES,
  30, YES,
  10, YES,
  40, SNAKE,
  0, END
  };
*/

void setup() {

  Serial.begin(9600);
  Serial.println("OpenSnake Firmware Version 1.2");

  pinMode(4, OUTPUT); // buzzer low side (simon says kit)
  digitalWrite(4, LOW);   // note, other size fo buzzer is 7, and we will call that in tone, later.

  pinMode(RED_LED_pin, OUTPUT); // "NO LED"
  digitalWrite(RED_LED_pin, LOW);
  pinMode(GREEN_LED_pin, OUTPUT); // "YES LED"
  digitalWrite(GREEN_LED_pin, LOW);

  // buttons
  pinMode(RECORD_BUTTON, INPUT_PULLUP);
  pinMode(PLAY_BUTTON, INPUT_PULLUP);
  pinMode(TRACK_SELECT_BUTTON, INPUT_PULLUP);
  pinMode(YES_BUTTON, INPUT_PULLUP);
  pinMode(NO_BUTTON, INPUT_PULLUP);
  pinMode(SNAKE_BUTTON, INPUT_PULLUP);

  pinMode(SERVO_PWR_CONTROL_PIN, OUTPUT); //
  digitalWrite(SERVO_PWR_CONTROL_PIN, LOW);

  // check for fresh IC. If so, then do a factory reset
  if (EEPROM.read(EEPROM_LOCATION_AUTOPLAY) == 255) // fresh ICs have all of their EEPROM values at 255, so we only need to check one location
  {
    factory_reset();
    // to indicate that we've done a "1st time" factory reset.
    // aka this is no longer a fresh IC.
  }

  // check for manual factory reset - user must hold down "REC" button through a power cycle,
  // then continue to hold down for 3 seconds
  int time_pressed = 0;
  while ( (check_buttons() == true) && (userInput == RECORD_CMD) ) // user must hold down record for 3 seconds
  {
    blink_led(RED_LED_pin);
    delay(1000);
    time_pressed++;
    if (time_pressed == 3)
    {
      factory_reset();
      break;
    }
  }

  // check for autoplay toggle on/off - user must hold down "PLAY" button through a power cycle,
  // then continue to hold down for 3 seconds
  time_pressed = 0;
  while ( (check_buttons() == true) && (userInput == PLAY_CMD) ) // user must hold down play for 3 seconds
  {
    blink_led(GREEN_LED_pin);
    delay(1000);
    time_pressed++;
    if (time_pressed == 3)
    {
      toggle_autoplay_onoff();
      break;
    }
  }

  // check for production testing method - user must hold down "YES" button through a power cycle,
  // then continue to hold down for 200 milliseconds
  time_pressed = 0;
  while ( (check_buttons() == true) && (userInput == YES_CMD) ) // user must hold down yes for 200ms
  {
    blink_led(GREEN_LED_pin);
    delay(100);
    time_pressed++;
    if (time_pressed == 2)
    {
      production_testing();
      break;
    }
  }

  if (EEPROM.read(EEPROM_LOCATION_AUTOPLAY) == AUTOPLAY_ON)
  {
    Serial.println("Autoplay on.");
    play_track();
    while (1);
  }

  byte track = EEPROM.read(EEPROM_LOCATION_TRACK);
  Serial.println("Autoplay off.");
  Serial.print("Current track ");
  Serial.println(track);
  blink_track(track);

  //print_EEPROM();

  //set_track(1);

  //play_track();

  //while (1);
}

void loop()
{
  if (check_buttons() == true)
  {
    switch (userInput) {
      case RECORD_CMD:
        if (recordButtonCounter > 200) record_track(); // require the user to hold it down for 2 seconds
        break;
      case PLAY_CMD:
        play_track();
        break;
      case TRACK_CMD:
        if (incrementTrackButtonCounter > 200) increment_track(); // require the user to hold it down for 2 seconds
        break;
      case SNAKE_CMD:
        if (snakeButtonCounter > 200) snake(); // requires the user to hold it down for 2 seconds
        break;
      default:
        Serial.print("Invalid userInput: ");
        Serial.println(userInput);
        break;
    }
  }
  delay(10); // button debounce
}

boolean play_track()
{
  byte track = EEPROM.read(EEPROM_LOCATION_TRACK);

  Serial.print("Playing track ");
  Serial.println(track);

  // First, find track length
  // scan through all memory locations for the track,
  // look for END event type, then store it in local
  // variable, use it later for playback for loop

  int start_mem_location = get_start_mem_location(track);

  Serial.print("start_mem_location: ");
  Serial.println(start_mem_location);

  // Play back the track
  byte event_type = 0; // yes, no, snake, end
  int event_delay = 0; // milliseconds 0-2550

  for (int pos = start_mem_location ; pos <= (start_mem_location + 99) ; pos += 2) // because each event has a timestamp and type, we increment 2
  {
    event_delay = int(EEPROM.read(pos));
    event_type = EEPROM.read(pos + 1); // the following memory location is type

    Serial.print("event_delay: ");
    Serial.println(event_delay);

    event_delay *= 100; // convert to milliseconds
    delay(event_delay);

    //Serial.print("event_type: ");
    //Serial.println(event_type);

    switch (event_type) {
      case YES:
        Serial.println("YES");
        yes();
        break;
      case NO:
        Serial.println("NO");
        no();
        break;
      case SNAKE:
        Serial.println("SNAKE");
        snake();
        break;
      case LAUGH:
        Serial.println("LAUGH");
        laugh();
        break;
      case CRY:
        Serial.println("CRY");
        cry();
        break;
      case HAPPY:
        Serial.println("HAPPY BIRTHDAY");
        happy_birthday();
        break;
      case END:
        Serial.println("END");
        break;
      default:
        Serial.println("Invalid event type!");
        break;
    }

    if (event_type == END) break;
  }

}


void yes()
{
  digitalWrite(GREEN_LED_pin, HIGH);
  digitalWrite(RED_LED_pin, LOW);
  for (int note = 150 ; note < 4000 ; note += 150)
  {
    tone(BUZZER_PIN, note, 40);
    delay(30);
  }
  noTone(BUZZER_PIN);
  digitalWrite(GREEN_LED_pin, LOW);
}

void no()
{
  digitalWrite(RED_LED_pin, HIGH);
  digitalWrite(GREEN_LED_pin, LOW);
  for (int note = 4000 ; note > 150 ; note -= 150)
  {
    tone(BUZZER_PIN, note, 30);
    delay(20);
  }
  noTone(BUZZER_PIN);
  digitalWrite(RED_LED_pin, LOW);
}

void snake()
{
  digitalWrite(SERVO_PWR_CONTROL_PIN, HIGH);   // turn on servo power

  myservo.attach(SERVO_PWM_PIN);  // attaches the servo on pin # to the servo object

  myservo.write(180); // move servo to open lid position

  // make siren sounds and blink red/green leds!!
  for (int i = 0 ; i <= 3 ; i++)
  {
    digitalWrite(RED_LED_pin, HIGH);
    digitalWrite(GREEN_LED_pin, LOW);
    for (int note = 150 ; note < 4000 ; note += 150)
    {
      tone(BUZZER_PIN, note, 30);
      delay(10);
    }
    digitalWrite(RED_LED_pin, LOW);
    digitalWrite(GREEN_LED_pin, HIGH);
    for (int note = 4000 ; note > 150 ; note -= 150)
    {
      tone(BUZZER_PIN, note, 30);
      delay(10);
    }
  }

  noTone(BUZZER_PIN);

  digitalWrite(RED_LED_pin, LOW);
  digitalWrite(GREEN_LED_pin, LOW);

  myservo.detach();  // detach() servo control pin

  digitalWrite(SERVO_PWR_CONTROL_PIN, LOW); // turn off servo power
}

void factory_reset()
{
  Serial.println("Factory Reset!!");

  // indicate a flashing of red/green (X3) to show user it's happening
  blink_led(RED_LED_pin);
  blink_led(GREEN_LED_pin);
  blink_led(RED_LED_pin);
  blink_led(GREEN_LED_pin);
  blink_led(RED_LED_pin);
  blink_led(GREEN_LED_pin);

  // store default track number in EEPROM location 0
  EEPROM.write(EEPROM_LOCATION_TRACK, 1);

  EEPROM.write(EEPROM_LOCATION_AUTOPLAY, AUTOPLAY_OFF); // turn autoplay off

  // store example tracks in track EEPROM locations

  // example track 1
  for (int i = 0 ; i < sizeof(example_track_1) ; i++)
  {
    EEPROM.write( 1 + i, example_track_1[i]); // starts at address 1
    if (example_track_1[i] == END) break;
  }

  //  // example track 2
  //  for (int i = 0 ; i < sizeof(example_track_2) ; i++)
  //  {
  //    EEPROM.write( 100 + i, example_track_2[i]); // starts at address 100
  //    if (example_track_2[i] == END) break;
  //  }
  //
  //  // example track 3
  //  for (int i = 0 ; i < sizeof(example_track_3) ; i++)
  //  {
  //    EEPROM.write( 200 + i, example_track_3[i]); // starts at address 200
  //    if (example_track_3[i] == END) break;
  //  }
  while (check_buttons() == true); // wait for release (aka debouce)
}

void print_EEPROM()
{
  // read a byte from the current address of the EEPROM
  int address = 0;
  int eeprom_length = EEPROM.length();
  for (int address = 0 ; address < eeprom_length ; address++)
  {
    Serial.print(address);
    Serial.print("\t");
    Serial.print(EEPROM.read(address), DEC);
    Serial.println();
  }
}

void set_track(byte track)
{
  EEPROM.write(EEPROM_LOCATION_TRACK, track); // store it in special EEPROM location for reading at play_track
  // and to save through a power cycle.
}

void increment_track()
{
  Serial.println("Incrementing track...");
  byte track = EEPROM.read(EEPROM_LOCATION_TRACK);
  track++;
  if (track == 6) track = 1; // loop back to track 1 (we only have EEPROM room for 5 total tracks)
  Serial.print("track: ");
  Serial.println(track);
  blink_track(track);
  set_track(track);
}

void blink_track(byte times)
{
  delay(1000);
  for (byte i = 0 ; i < times ; i++)
  {
    digitalWrite(RED_LED_pin, HIGH);
    delay(100);
    digitalWrite(RED_LED_pin, LOW);
    delay(500);
  }
}

void blink_led(byte pin)
{
  digitalWrite(pin, HIGH);
  delay(100);
  digitalWrite(pin, LOW);
}

boolean check_buttons()
{
  userInput = 0;
  if (digitalRead(RECORD_BUTTON) == true) recordButtonCounter = 0; // user released record button, reset counter
  if (digitalRead(TRACK_SELECT_BUTTON) == true) incrementTrackButtonCounter = 0; // user released track sel button, reset counter
  if (digitalRead(SNAKE_BUTTON) == true) snakeButtonCounter = 0; // user released snake button, reset counter

  if (digitalRead(PLAY_BUTTON) == false) userInput = PLAY_CMD;
  else if (digitalRead(RECORD_BUTTON) == false) // RECORD (note, requires long press)
  {
    recordButtonCounter++;
    userInput = RECORD_CMD;
  }
  else if (digitalRead(TRACK_SELECT_BUTTON) == false) // increment track (note, requires long press)
  {
    incrementTrackButtonCounter++; // needed to know if it is gonna be a long press
    if (digitalRead(YES_BUTTON) == false) userInput = LAUGH_CMD; // "shift yes" (aka track_select + yes) = laugh
    else if (digitalRead(NO_BUTTON) == false) userInput = CRY_CMD; // "shift no" (aka track_select + no) = cry
    else if (digitalRead(SNAKE_BUTTON) == false) userInput = HAPPY_CMD; // "shift snake" (aka track_select + snake) = happy birthday
    else userInput = TRACK_CMD; // if no other buttons are held down a the same time, then it's just a plain old "track select command".
  }
  else if (digitalRead(YES_BUTTON) == false) userInput = YES_CMD;
  else if (digitalRead(NO_BUTTON) == false) userInput = NO_CMD;
  else if (digitalRead(SNAKE_BUTTON) == false)
  {
    snakeButtonCounter++;
    userInput = SNAKE_CMD;
  }
  if (userInput) return true;
  else return false;
}
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

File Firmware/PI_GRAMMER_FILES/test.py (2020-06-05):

# Raspberry Pi stand alone AVR programmer
# SparkFun Electronics
# Pete Lewis 7/1/2016
# More about Avrdude install/setup/use can be found at
# https://learn.adafruit.com/program-an-avr-or-arduino-using-raspberry-pi-gpio-pins/

# This python script bassically does this:
# Press a button to engage programming
# Programming BASH file is called pi_program.sh
# This contains all the calls to avrdude, including firmware, fuses and other flags
# Indicate status on a few LEDs - ideally we can show success at fuse bits, program, and lock bits.

import os, sys
import shutil
import serial
import time
import RPi.GPIO as GPIO
import filecmp

STAT = 7
FUSE_P = 15
FUSE_F = 13
FLASH_P = 31
FLASH_F = 11
LOCK_P = 32
LOCK_F = 22
SERIAL_P = 16
SERIAL_F = 18
PGM_SWITCH = 36

CAPSENSE = 33
SHUTDOWN = 29

STATLED_ON = False # Used for toggling stat led on and off during main loop

GPIO.setwarnings(False)
GPIO.setmode(GPIO.BOARD)

GPIO.setup(STAT, GPIO.OUT)
GPIO.setup(FUSE_P, GPIO.OUT)
GPIO.setup(FUSE_F, GPIO.OUT)
GPIO.setup(FLASH_P, GPIO.OUT)
GPIO.setup(FLASH_F, GPIO.OUT)
GPIO.setup(LOCK_P, GPIO.OUT)
GPIO.setup(LOCK_F, GPIO.OUT)
GPIO.setup(SERIAL_P, GPIO.OUT)
GPIO.setup(SERIAL_F, GPIO.OUT)
GPIO.setup(PGM_SWITCH, GPIO.OUT)

GPIO.setup(SHUTDOWN, GPIO.IN, pull_up_down=GPIO.PUD_UP) # with internal pullup enabled - trying this out to avoid accidental shutdowns.
#GPIO.setup(SHUTDOWN, GPIO.IN) # NO INTERNAL PULLUP
GPIO.setup(CAPSENSE, GPIO.IN)

GPIO.output(STAT, GPIO.LOW)
GPIO.output(FUSE_P, GPIO.LOW)
GPIO.output(FUSE_F, GPIO.LOW)
GPIO.output(FLASH_P, GPIO.LOW)
GPIO.output(FLASH_F, GPIO.LOW)
GPIO.output(LOCK_P, GPIO.LOW)
GPIO.output(LOCK_F, GPIO.LOW)
GPIO.output(SERIAL_P, GPIO.LOW)
GPIO.output(SERIAL_F, GPIO.LOW)
GPIO.output(PGM_SWITCH, GPIO.LOW) # LOW is OFF, this is active high, hardware has 10K pullup

firmware_path_media = ' '
new_hex = False
copy_flag = False

bash_path_media = ' '
new_bash = False
copy_flag_bash = False

test_dot_py_path_media = ' '
new_test_dot_py = False
copy_flag_test_dot_py = False

stat_blink_counter = 0

LOCK_BITS_PASS = False #Used to know if lock bits programming passed or failed, and then determine if we should even both carrying on with Serial upload attempts

def all_leds_on():
        GPIO.output(STAT, GPIO.HIGH)
        GPIO.output(FUSE_P, GPIO.HIGH)
        GPIO.output(FUSE_F, GPIO.HIGH)
        GPIO.output(FLASH_P, GPIO.HIGH)
        GPIO.output(FLASH_F, GPIO.HIGH)
        GPIO.output(LOCK_P, GPIO.HIGH)
        GPIO.output(LOCK_F, GPIO.HIGH)
        GPIO.output(SERIAL_P, GPIO.HIGH)
        GPIO.output(SERIAL_F, GPIO.HIGH)

def all_leds_off():
        GPIO.output(STAT, GPIO.LOW)
        GPIO.output(FUSE_P, GPIO.LOW)
        GPIO.output(FUSE_F, GPIO.LOW)
        GPIO.output(FLASH_P, GPIO.LOW)
        GPIO.output(FLASH_F, GPIO.LOW)
        GPIO.output(LOCK_P, GPIO.LOW)
        GPIO.output(LOCK_F, GPIO.LOW)
        GPIO.output(SERIAL_P, GPIO.LOW)
        GPIO.output(SERIAL_F, GPIO.LOW)

def blink_circle():
        GPIO.output(FUSE_P, GPIO.HIGH)
        time.sleep(.1)
        GPIO.output(FUSE_P, GPIO.LOW)
        GPIO.output(FLASH_P, GPIO.HIGH)
        time.sleep(.1)
        GPIO.output(FLASH_P, GPIO.LOW)
        GPIO.output(LOCK_P, GPIO.HIGH)
        time.sleep(.1)
        GPIO.output(LOCK_P, GPIO.LOW)
        GPIO.output(LOCK_F, GPIO.HIGH)
        time.sleep(.1)
        GPIO.output(LOCK_F, GPIO.LOW)
        GPIO.output(FLASH_F, GPIO.HIGH)
        time.sleep(.1)
        GPIO.output(FLASH_F, GPIO.LOW)        
        GPIO.output(FUSE_F, GPIO.HIGH)
        time.sleep(.1)
        GPIO.output(FUSE_F, GPIO.LOW)
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

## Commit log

2017-10-10 Initial layout and code
    Note, this code is for a demo that using a light sensor on pin A0, and
    so isn't *exactly* compatible with v01 of hardware. The plan for the
    default code/mode will include an RC receiver being the trigger method.
    [OpenSnake.brd, OpenSnake.sch]
2017-10-27 Moving light sensor to look for delta
    This is now triggered by a delta (change downward) in light. So it will
    hopefully work in various light settings. The previous code had a hard
    threshold for the trigger, and so would accidentally trigger in low
    light settings.
2017-10-30 added in some debouncing on light sensor
    this seems to work better in lower light settings where the ADC may only
    return 10 or so and then only drop 5 units when you cover it up.
    The "count" variable and feature helps ensure that the noise doesn't
    cause accidental pops, and requires that the person hold their hand over
    the sensor and the reading stay "low" for at least 60 reads (with is
    roughly 120 ms - i think)
    [OpenSnake.ino]
2020-01-11 Lid designs ready for cutting
    [Lid.brd, Lid.dxf, Lid_TOP.dxf]
2020-01-12 widened hole and moved to 1/4" for everything (except top lid)
    [Lid.brd]
2020-01-12 removing old dxf files
    also scooted reference line out to show middle bracer is aligned, and removed second lid dia package cause it's no longer needed.
    [Lid.brd, Lid.dxf, Lid_TOP.dxf]
2020-01-13 Final design on lid
    Tweaked the tightness on all the parts to fit snugly with the 1/4" acrylic (two prints at 10/100/5000). Also tweaked the drill hits to allow 4-40 to pass through easily and sevro screws to bite just a little.
    [Lid.brd]
2020-01-14 initial idea on pcb layout
    the plan is to use some double sided tape and stick this to the side of the can. The 9V battery would also be stuck to the other side.
    [OpenSnake.brd, OpenSnake.sch]
2020-01-21 v01 hardware ordered - Added mario logo to bottom silk - and code started
    -mario logo on bottom silk
    -v01 hardware prototypes ordered
    -Started working on the code using a simon says kit.
    -got yes, no sound functions working
    -got default tracks working and playing
    -still needs servo control implemented, but currently mapped out in snake() function
    -still needs button control, record feature and factory reset feature
    [OpenSnake.sch]
2020-02-09 Servo current spike measurements, mario graphic backup
2020-02-10 starting button control, track increment working
2020-02-16 created record_track() - not tested on hardware yet
    also created get_start_mem_location(byte track) to a function, becuase both play_track and record_track need this. Might consider moving "track" to a global variable in the future, but currently read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
    **Still need to truncate and format event_delay before sending it to record_event()
2020-02-26 Adjusted tValues for better assembly sheet, created assembly sheet PDF
    [OpenSnake.brd, OpenSnake.sch]
2020-02-27 Corrected RX/TX to 6-pin Serial programming header
    I had these swapped on the header. Classic rookie mistake :)
    -Swapped RX/TX on the serial header
    -bumped version to v10 in sch and brd copper
    [OpenSnake.brd, OpenSnake.sch]
2020-02-27 Optiboot hex file and added fuse settings at top of sketch
2020-02-27 Code updates for v01
    -adjusted pin definitions to work with v01 hardware. track select and play verified.
    -added in servo power control functionality, attach and detach
    -corrected comments on example 1
    -tweaked example 2 to show yes and no
    -added debug on startup to show current track, to verify that it sticks through a power cycle. It does.
    -commented out factory reset for now, during dev
    -added buzzer pin define and used it in yes and no functions
    -corrected get_start_mem_location(), it was never tested, and was causing compile errors because I needed to actually return the location properly.
    [OpenSnake.ino]
2020-02-29 recording working wahoo!!
    note, I switched the buzzer pin to an unused pin during dev work. This will need to be changed back to 8 for it to work with v01 hardware.
    debounce on buttons working pretty good with initial testing. Went with a "wait for release" style. This may need to be tweaked in the future, but seems good as is for now.
    [OpenSnake.ino]
2020-03-02 Factory reset caused by fresh IC or holding REC down through a pwr cycle
    [OpenSnake.ino]
2020-03-11 final changes to v10
    -added green LED
    -added silk labels for servo ports
    -Panelized and cammed
    [OpenSnake-Panel.GBL, OpenSnake-Panel.GBO, OpenSnake-Panel.GBP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]
2020-03-30 GREEN LED support and blink track in setup
2020-04-12 Adjusted example 1 to match video of routine 1
    [routine_1_times.ods]
2020-04-21 Rec and track sel button now require long press, plus more
    -to avoid accidental presses of record or track select, they now require a "long press", so the user must hold them down for about 2 seconds to register an intended press. This is because users will most likely press play in the middle of a performance, and we don't want them to accidentally press nearby buttons. Note, play is still instantly effective. Also note, YES, NO, and SNAKE are inactive unless recording.
    -factory reset now requires user to hold down for 3 seconds.
    -snake event now includes siren sounds and green/red led blinking.
    -removed example tracks 2 and 3, to avoid confusion.
    -Cleaned up and filled in header at top of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
    [OpenSnake.ino]
2020-05-08 Lid and flap done. Final versions in brd and dxf files
    [Lid.brd, Lid_FLAP_v3.dxf, Lid_v2.dxf]
2020-05-08 removed delay before servo detach/powerdown
    Servo moves to "open" position really quickly, so no need for this delay. When testing, I tried to move the servo during these 2 seconds, and was fighting the power/control. So I'm guessing other might do the same. Now the servo frees up immediately after it's done moving, to avoid this potential user issue.
    [OpenSnake.ino]
2020-06-05 corrected device type for production with atmega328 (note, no "p")
2020-07-08 lid panel files v3
    [Lid-v3-FLAP-Panel.brd, Lid-v3-FLAP-Panel.dxf, Lid-v3-FLAP-test_1_unit.brd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]
2020-07-29 Lid flap and hinge wall updates
    -moved flap arm inward 0.01 inch on both sides.
    -extended flab nubbins out 0.04 inch, to make them protrude into hinge holes a bit more.
    -mitered hard corners to help avoid cracking
    -enlarged hinge nubbin hole from 0.1 inch dia to 0.12 inch dia
    [Lid.brd]
2020-10-22 assembly sheet optimization
    -just positioning names and values so they print nicely
    [OpenSnake.brd, OpenSnake.sch]
2020-10-22 Lid "v4" finalized
    [Lid-v4-Panel.brd, Lid.brd]
2021-12-01 Lid and flap file cleanup
    [FLAP.dxf, FLAP_Panel.brd, LID.dxf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]
2021-12-01 v20 PCB layout - all SMD
    -Moved to high side switch with mosfet for servo power control, this will also come directly from battery (since it is now max 6V) to alleviate vreg
    -Switched to JST connector for batter input.
    -removed power switch, because the plan is to source a battery holder with switch.
    -moved to MIC5205 5V vreg, because it no longer has to power servo.
    -switched to test points for programming to make room.
    -SMD buzzer
    -SMD LEDs
    -SMD servo connectors
    [OpenSnake-Panel.brd, OpenSnake.brd, OpenSnake.sch]
2021-12-01 Firmware updates (v1.1)
    -Long press = snake pop (for servo horn installation)
    -If the user holds down the snake button for a "long press" (3+seconds), then the controller will move the servo to the open position. This is useful for first time setup when you need to attach the servo horn in the correct position.
    -incremented debug FW version number to v1.1
    -Use the "track select" button as a "shift" key to access laugh and cry sounds.
    -added leds to laugh and cry
    -Happy Birthday added as "track_select + snake"
    -Added autoplay feature, removed snake from happy birthday
    -added atribution and comments about v1.1 fw updates
    -adjusted AUTOPLAY so it is default OFF on update from v1.0.
    (V1.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
    [OpenSnake.ino]
2022-08-29 production testing added - FW v12
    -added a production testing method to more quickly test each feature of the device.

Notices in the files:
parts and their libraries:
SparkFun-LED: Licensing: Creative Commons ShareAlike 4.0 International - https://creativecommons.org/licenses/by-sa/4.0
